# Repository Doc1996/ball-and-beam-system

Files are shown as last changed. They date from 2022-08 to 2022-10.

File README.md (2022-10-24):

# Ball and Beam Control System

<br>

<p align="justify">&nbsp;&nbsp;&nbsp;&nbsp;&nbsp;&nbsp;&nbsp;&nbsp;To examine the possibility of controlling an inherently unstable and nonlinear system, in this project a ball and beam laboratory setup is designed and an appropriate ball position control system is implemented. The design of the laboratory setup includes the selection of the appropriate electronic and mechanical components, design of mechanical components that are not available, production of designed components and assembling all elements of the setup into a whole. The implementation of the ball position control system involves defining the input and output variables of the designed setup, identification of the mathematical model of the setup, designing a suitable variable estimator and designing a controller that will control the position of the ball on the beam.</p>

<br>

## Project workflow

<br>

<b>Step 1.</b>&nbsp;&nbsp;Designing and 3D printing the needed components
<br>
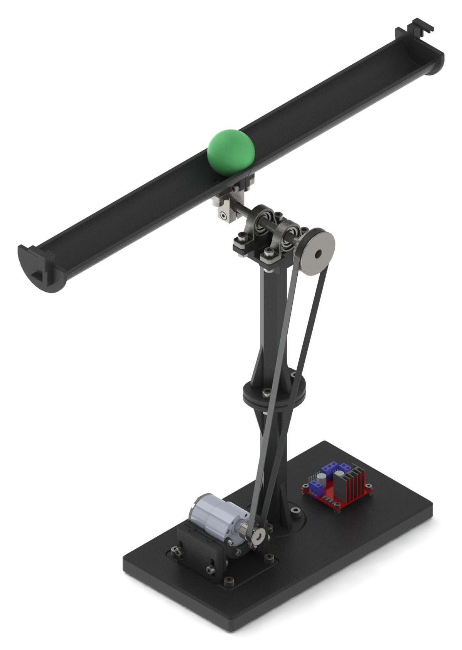
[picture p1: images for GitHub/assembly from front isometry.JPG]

<br>

<b>Step 2.</b>&nbsp;&nbsp;Assembling the components into a system
<br>
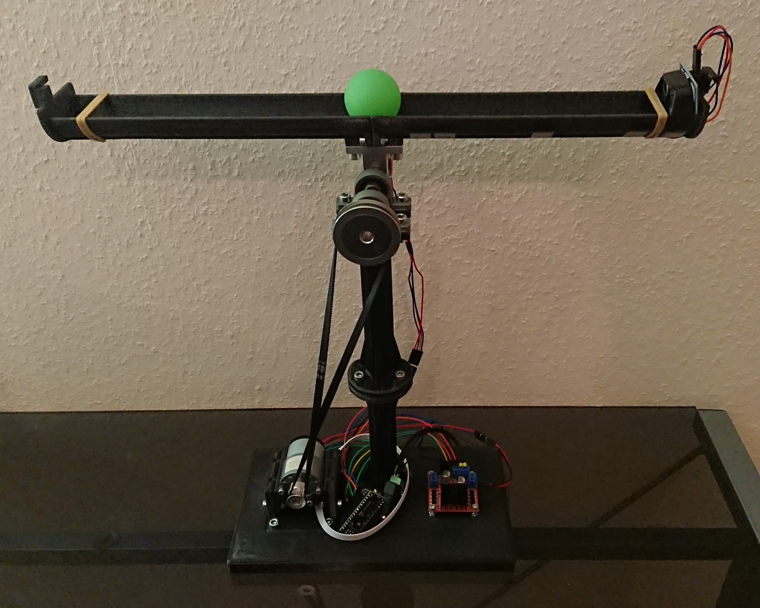
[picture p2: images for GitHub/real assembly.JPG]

<br>

<b>Step 3.</b>&nbsp;&nbsp;Identifying the motor model
<br>
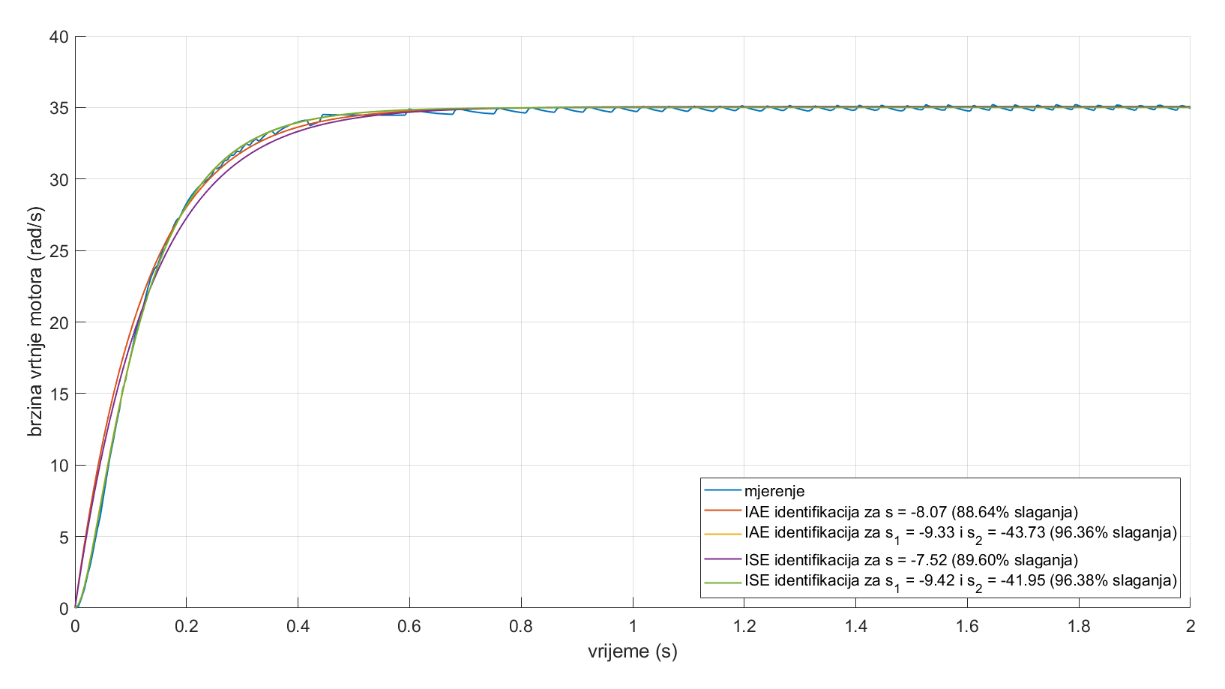
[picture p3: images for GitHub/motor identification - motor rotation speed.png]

<br>

<b>Step 4.</b>&nbsp;&nbsp;Modeling the ball and beam system
<br>
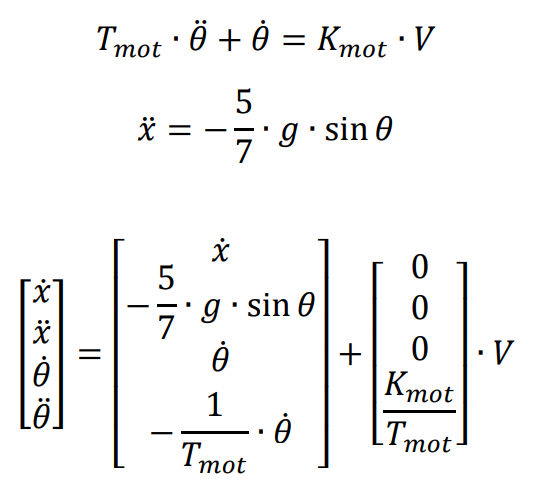
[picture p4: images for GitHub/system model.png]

<br>

<b>Step 5.</b>&nbsp;&nbsp;Designing the both low-pass filtering estimator and extended Kalman filter (EKF)
<br>
<br>

<b>Step 6.</b>&nbsp;&nbsp;Designing the both PD-PD cascade controller and state-space controller
<br>
<br>

<b>Step 7.</b>&nbsp;&nbsp;Modeling the motor static friction
<br>
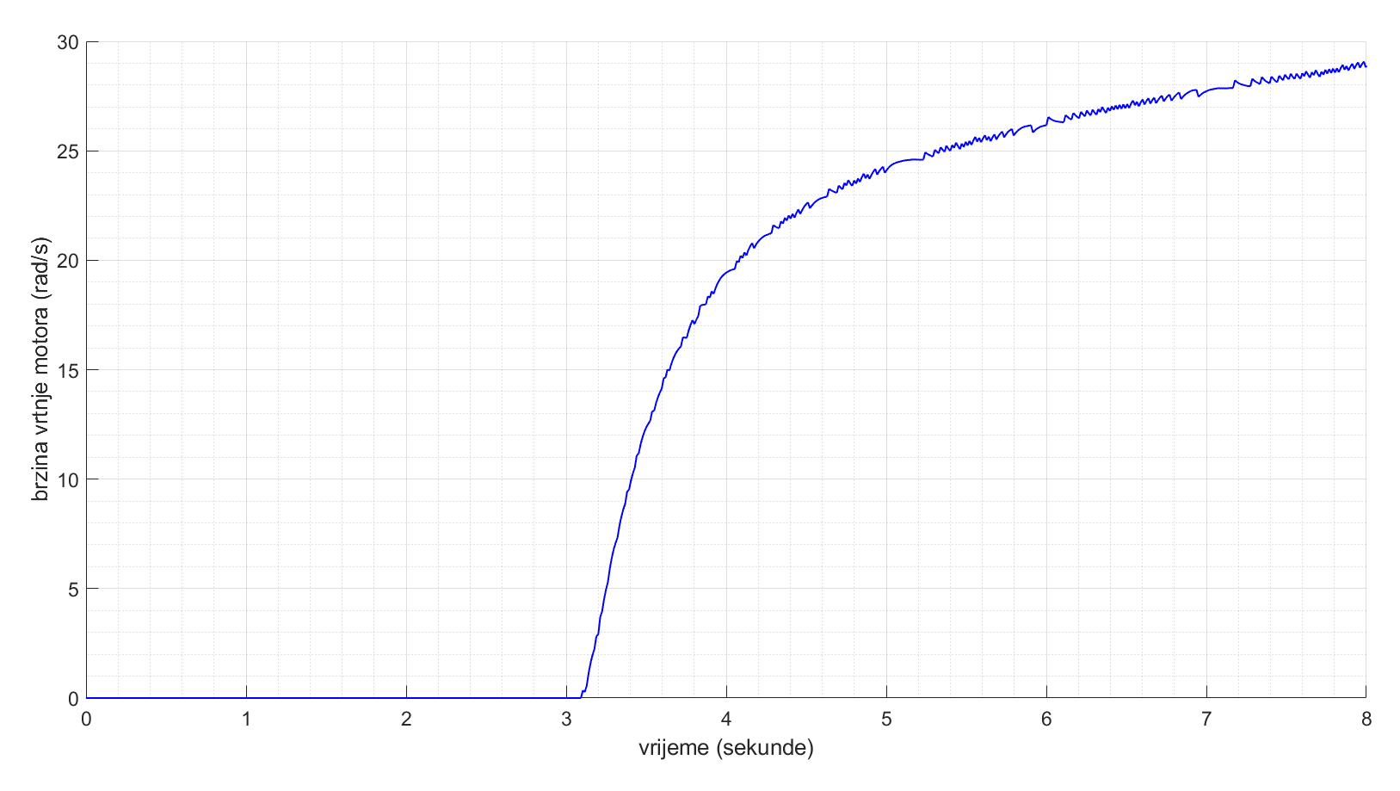
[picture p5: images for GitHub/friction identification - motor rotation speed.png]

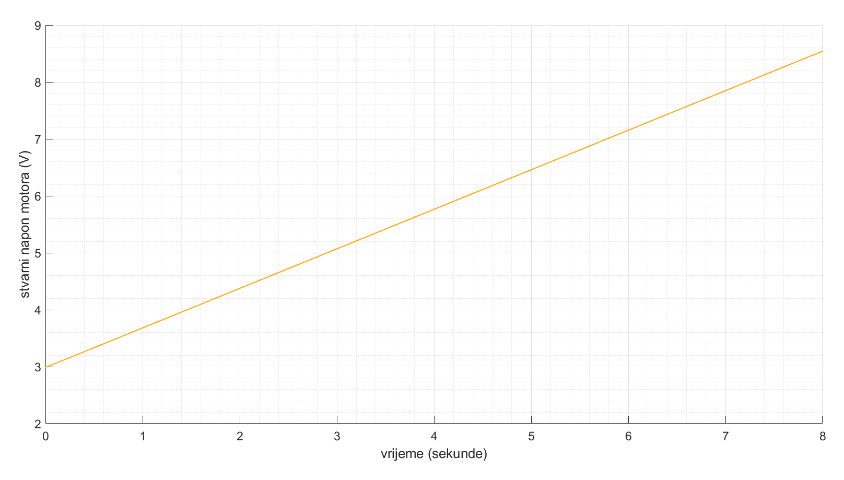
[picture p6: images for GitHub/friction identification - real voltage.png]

<br>

<b>Step 8.</b>&nbsp;&nbsp;Implementing the designed estimators and controllers on the Arduino Uno microcontroller
<br>
<br>

<b>Step 9.</b>&nbsp;&nbsp;Analyzing the results for disturbance compensation (shown for EKF and state-space controller)
<br>
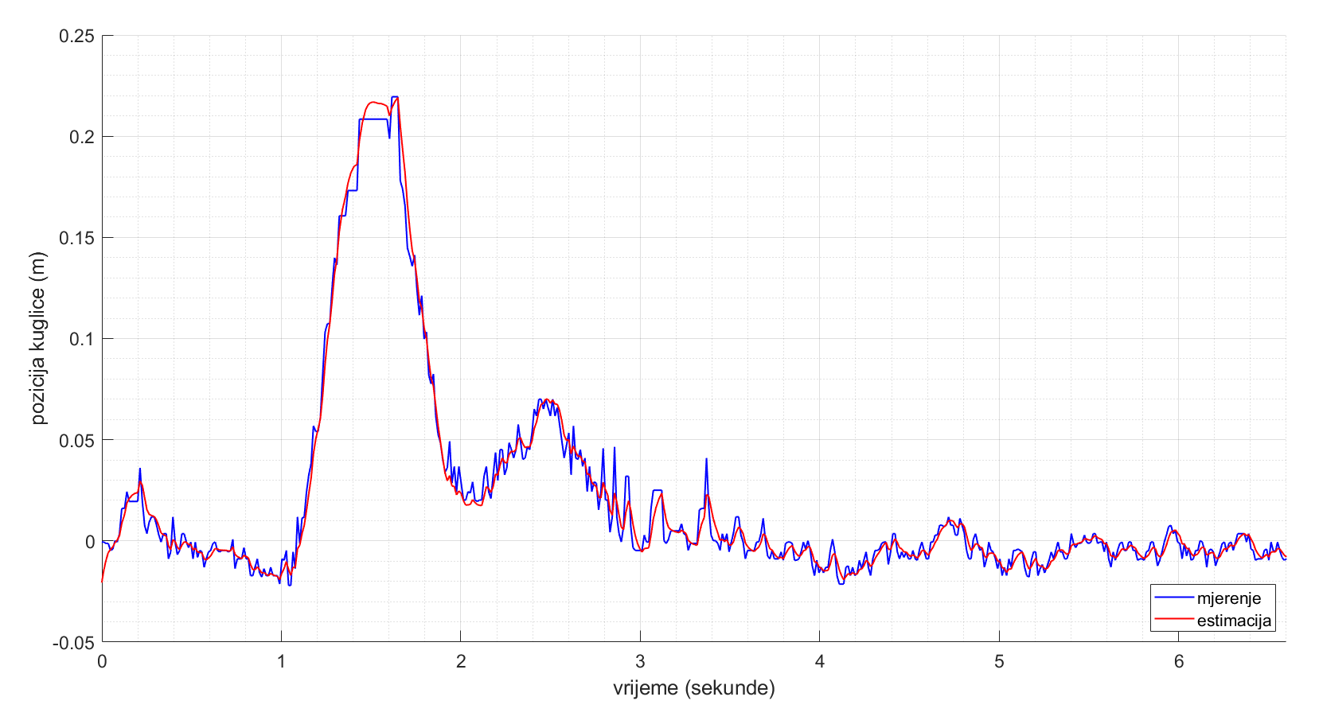
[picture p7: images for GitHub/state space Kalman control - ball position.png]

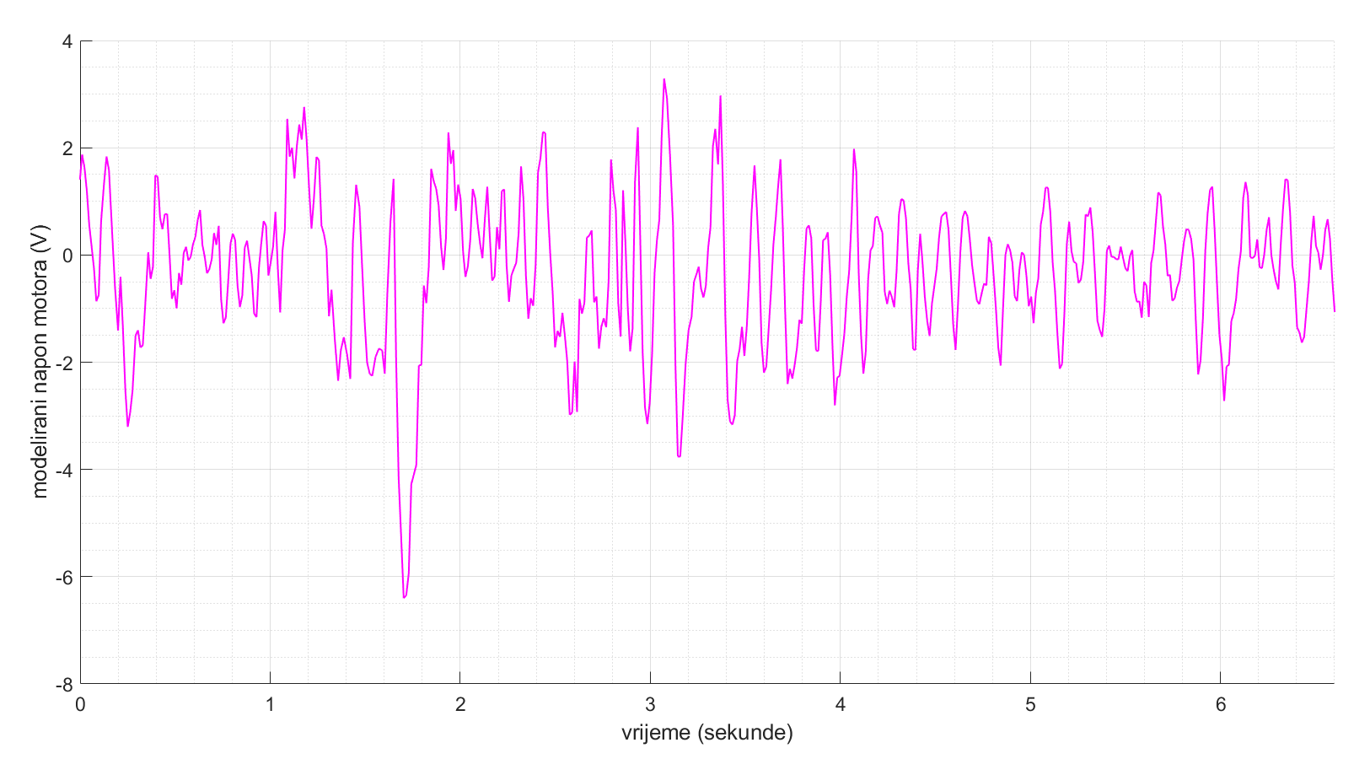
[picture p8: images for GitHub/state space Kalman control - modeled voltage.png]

<br>

<b>Step 10.</b>&nbsp;&nbsp;Analyzing the results for reference tracking (shown for EKF and state-space controller)
<br>
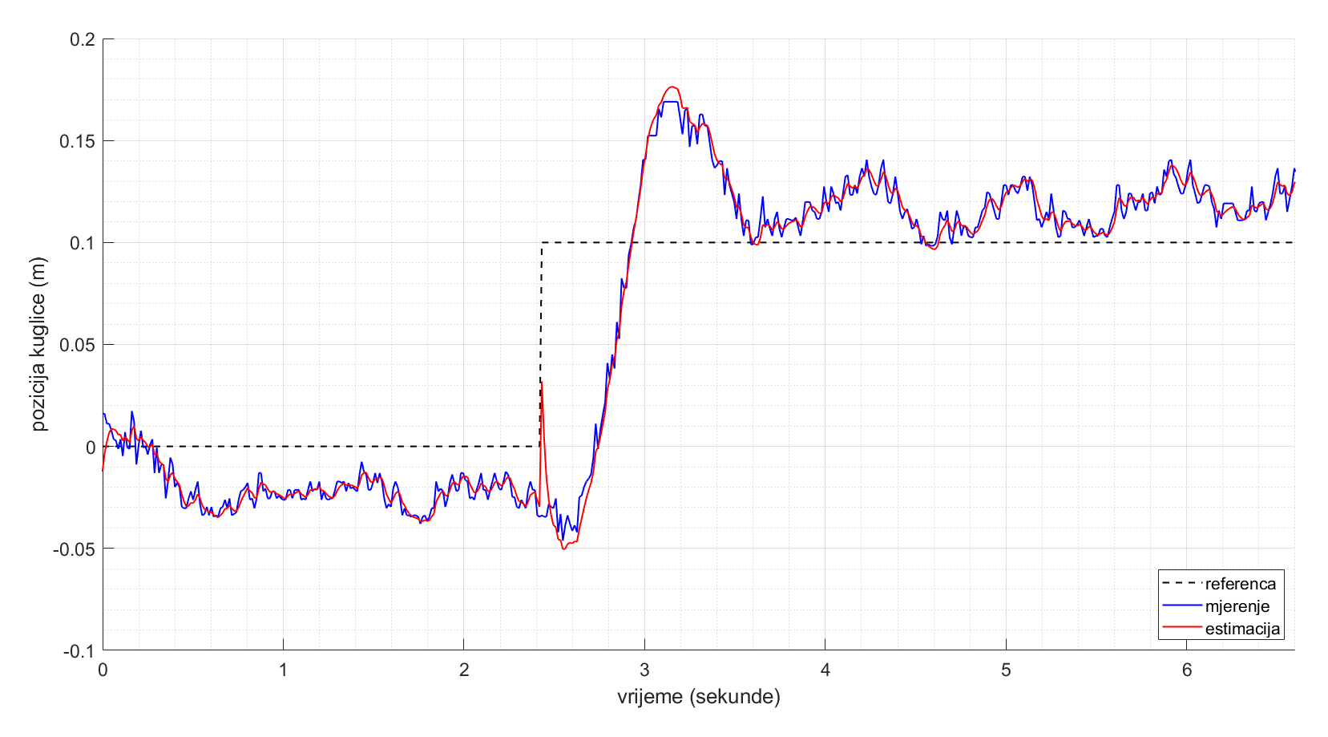
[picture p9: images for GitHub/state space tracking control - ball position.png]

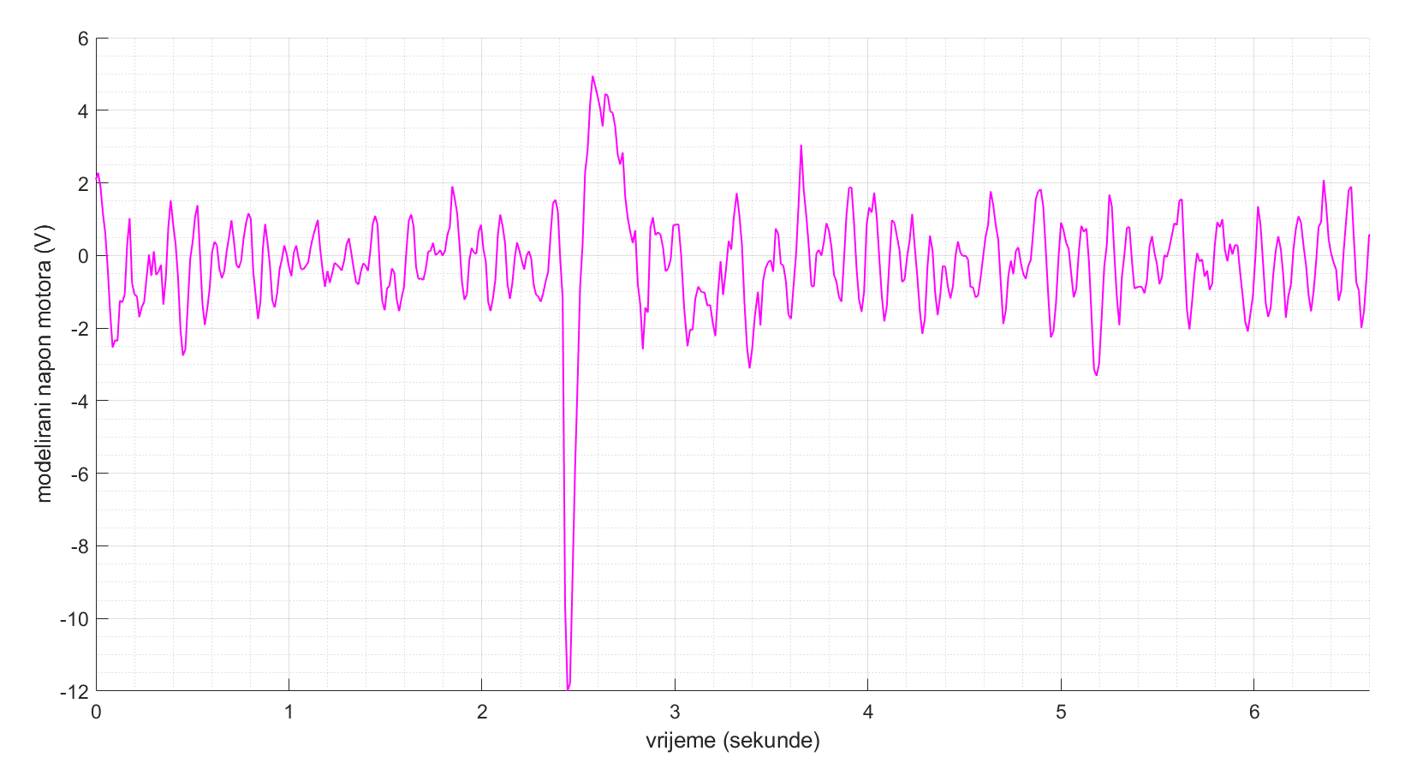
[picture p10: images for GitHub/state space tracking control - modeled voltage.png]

<br>

<b>Step 11.</b>&nbsp;&nbsp;Choosing the system with state-space controller and EKF due to best results
<br>
<br>

## Run the project on Windows

<br>

<b>Step 1.</b>&nbsp;&nbsp;Clone the repository:
<pre>
cd %HOMEPATH%

git clone https://github.com/Doc1996/ball-and-beam-system
</pre>
<br>

<b>Step 2.</b>&nbsp;&nbsp;Setup the Arduino IDE for using the Arduino Uno microcontroller
<br>
<br>

<b>Step 3.</b>&nbsp;&nbsp;Upload the Arduino project <i>system_control</i> to the microcontroller
<br>
<br>

<b>Optional step</b>&nbsp;&nbsp;Run the Matlab script <i>identify_and_control_model.m</i> and examine results
<br>
<br>

<b>Optional step</b>&nbsp;&nbsp;Run the Matlab script <i>plot_record_data.m</i> and examine results
<br>
<br>

## Run the project on Linux

<br>

<b>Step 1.</b>&nbsp;&nbsp;Clone the repository:
<pre>
cd $HOME

git clone https://github.com/Doc1996/ball-and-beam-system
</pre>
<br>

<b>Step 2.</b>&nbsp;&nbsp;Setup the Arduino IDE for using the Arduino Uno microcontroller
<br>
<br>

<b>Step 3.</b>&nbsp;&nbsp;Upload the Arduino project <i>system_control</i> to the microcontroller
<br>
<br>

<b>Optional step</b>&nbsp;&nbsp;Run the Matlab script <i>identify_and_control_model.m</i> and examine results
<br>
<br>

<b>Optional step</b>&nbsp;&nbsp;Run the Matlab script <i>plot_record_data.m</i> and examine results
<br>
<br>

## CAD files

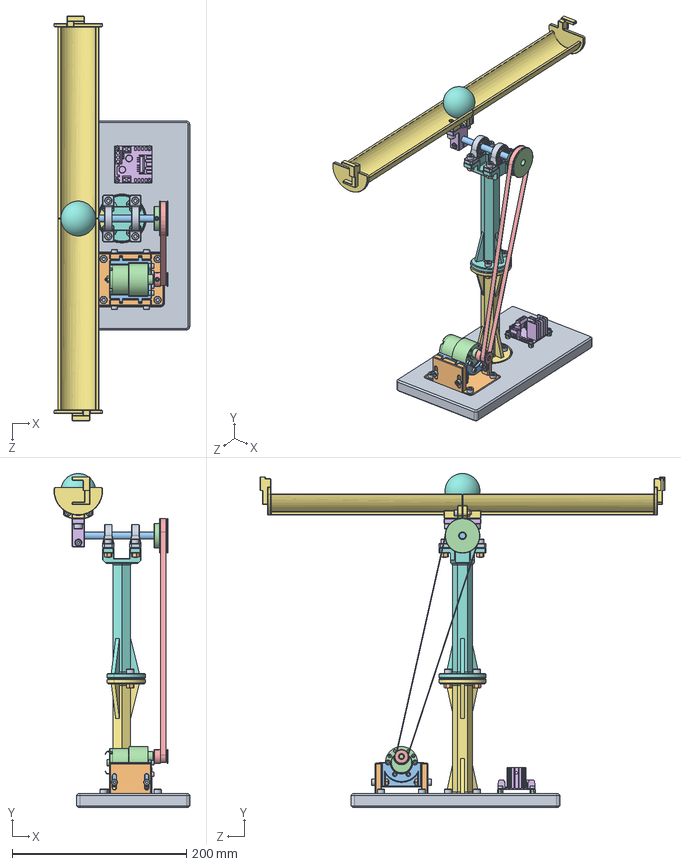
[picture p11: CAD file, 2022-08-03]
ball and beam model/ball and beam assembly.SLDASM
155.7 x 383.4 x 464.4 mm
mount
motor slider
motor frame
JGB37-520 motor
6mm 20-teeth gear
L298N driver
lower pillar
upper pillar
bearing frame x 2
ball bearing x 2
shaft
8mm 60-teeth gear
timing belt
holder
half guide x 2
ball
socket head cap screw_din x 30
hex nut style 1 gradeab_din x 19
socket set screw flat point_din x 4
hex nut style 1 gradeab_iso x 12

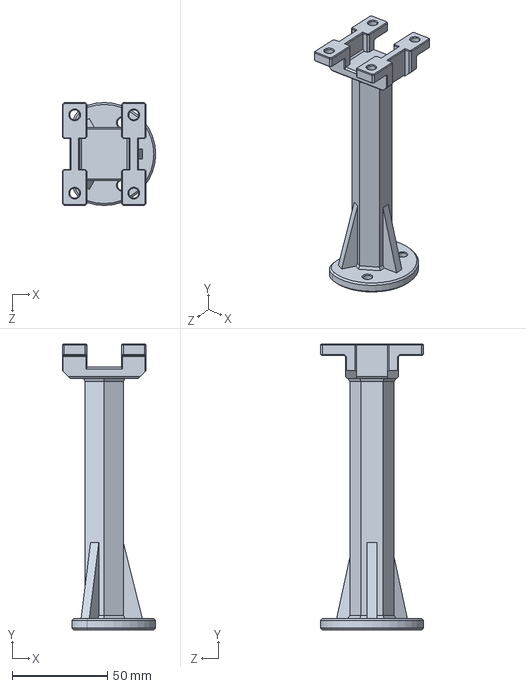
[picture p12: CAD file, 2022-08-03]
ball and beam model/upper pillar.SLDPRT
49.0 x 150.0 x 54.0 mm

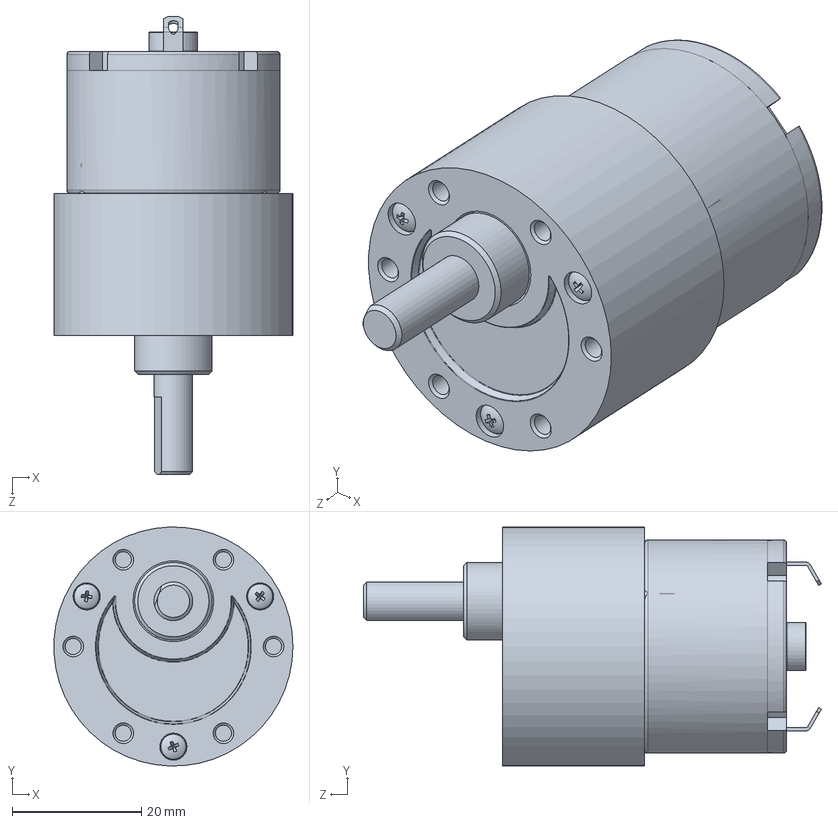
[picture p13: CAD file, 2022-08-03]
ball and beam model/JGB37-520 motor.SLDPRT
37.0 x 37.0 x 70.9 mm

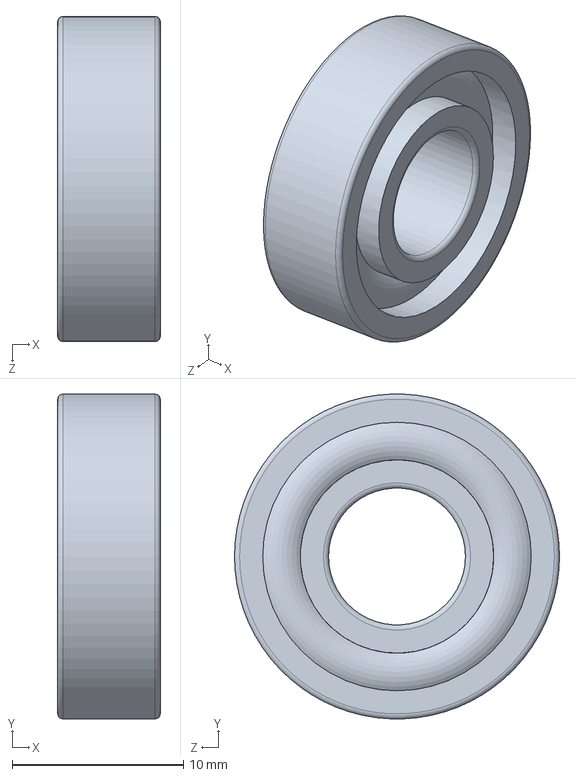
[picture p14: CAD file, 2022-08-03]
ball and beam model/ball bearing.SLDPRT
6.00 x 19.0 x 19.0 mm

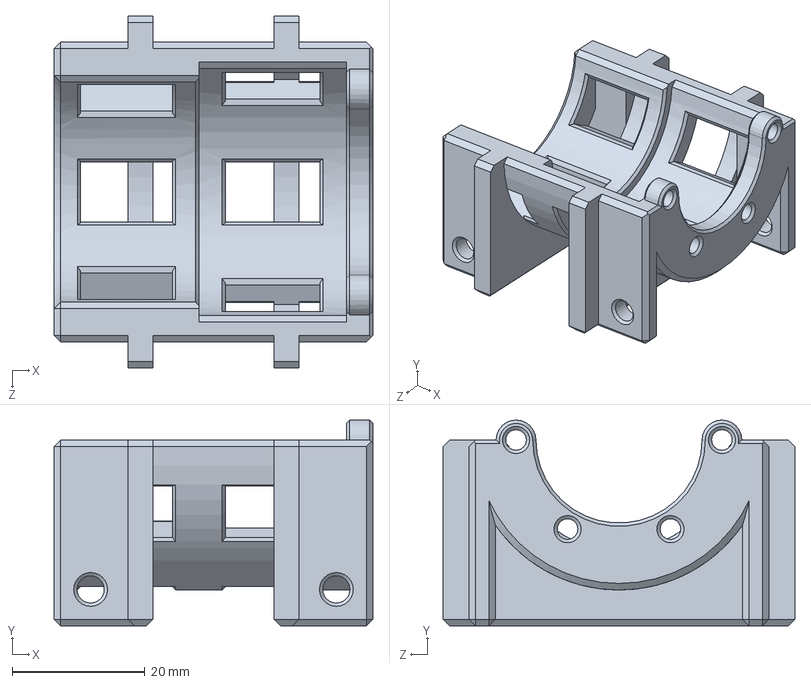
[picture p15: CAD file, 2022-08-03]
ball and beam model/motor frame.SLDPRT
48.0 x 31.0 x 53.0 mm

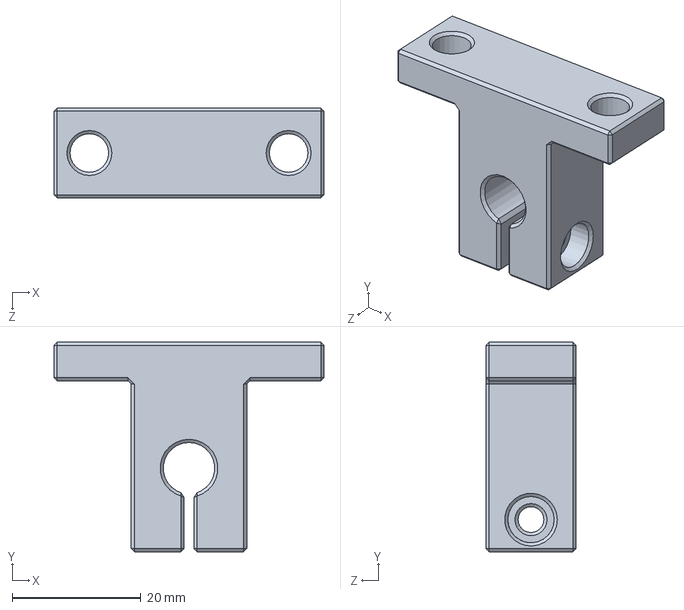
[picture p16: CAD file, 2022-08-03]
ball and beam model/holder.SLDPRT
42.0 x 32.6 x 14.0 mm

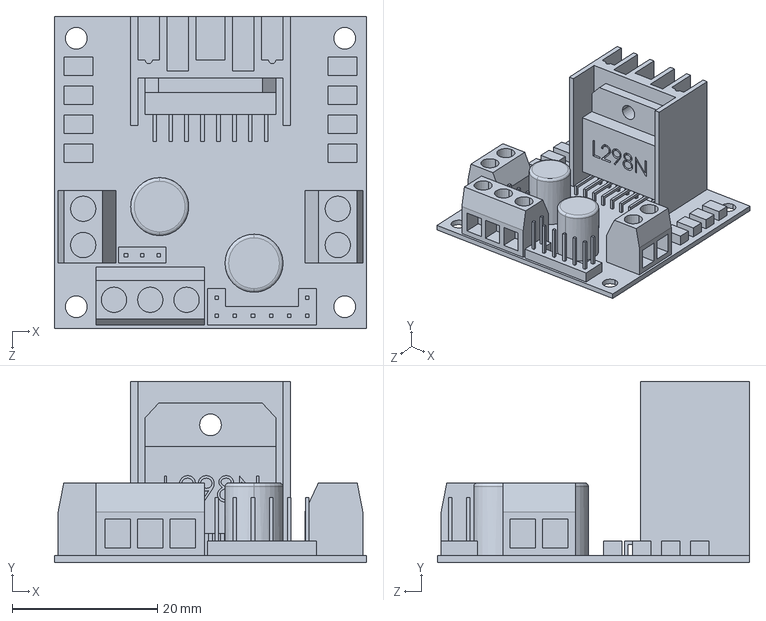
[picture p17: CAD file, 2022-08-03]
ball and beam model/L298N driver.SLDPRT
43.0 x 25.0 x 43.0 mm

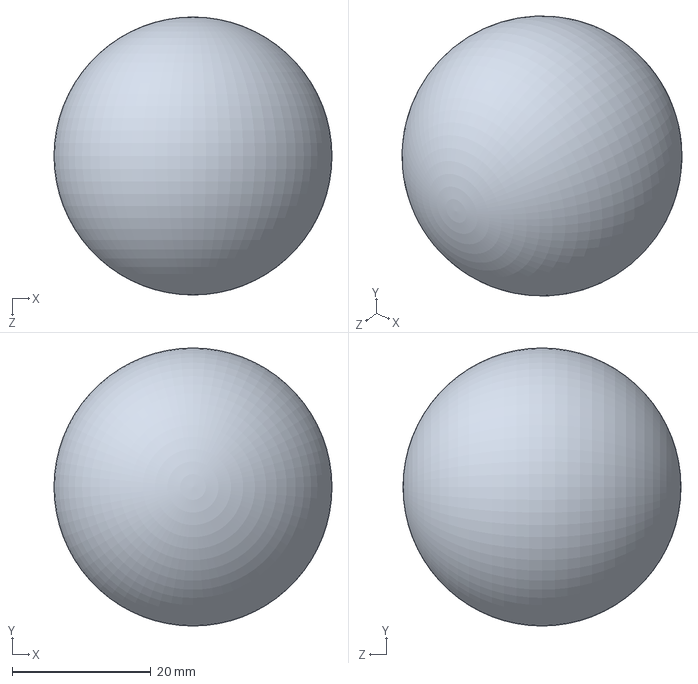
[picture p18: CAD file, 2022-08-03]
ball and beam model/ball.SLDPRT
40.0 x 40.0 x 40.0 mm

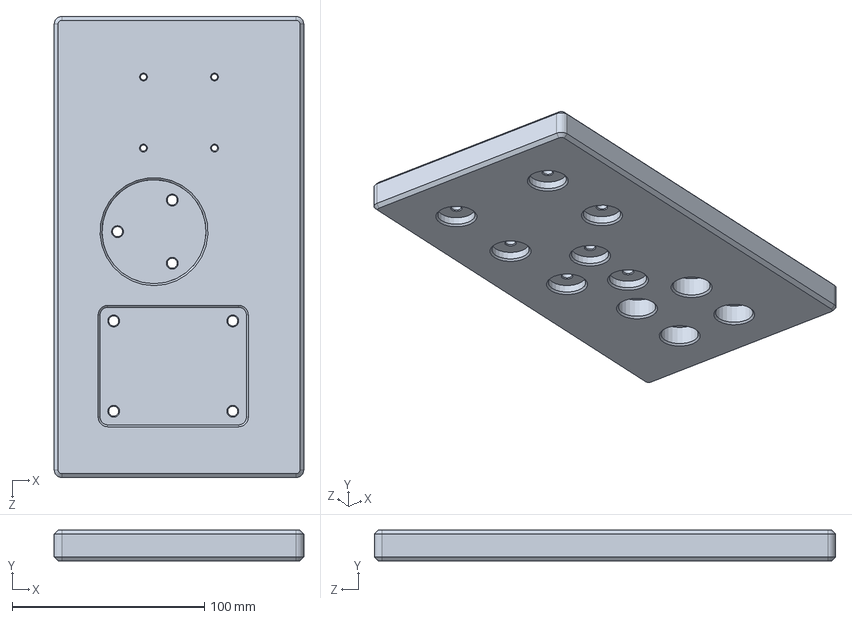
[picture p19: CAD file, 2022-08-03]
ball and beam model/mount.SLDPRT
130.0 x 16.0 x 240.0 mm

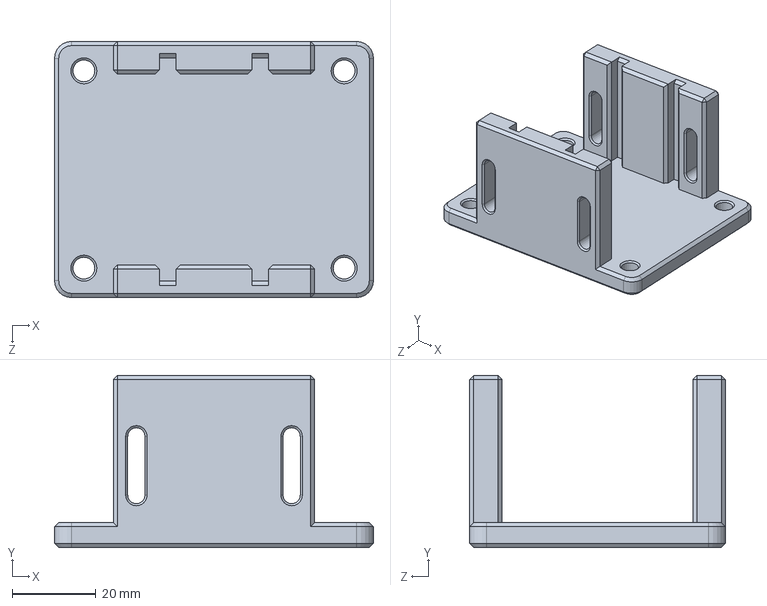
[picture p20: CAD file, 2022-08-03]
ball and beam model/motor slider.SLDPRT
76.0 x 41.0 x 61.0 mm

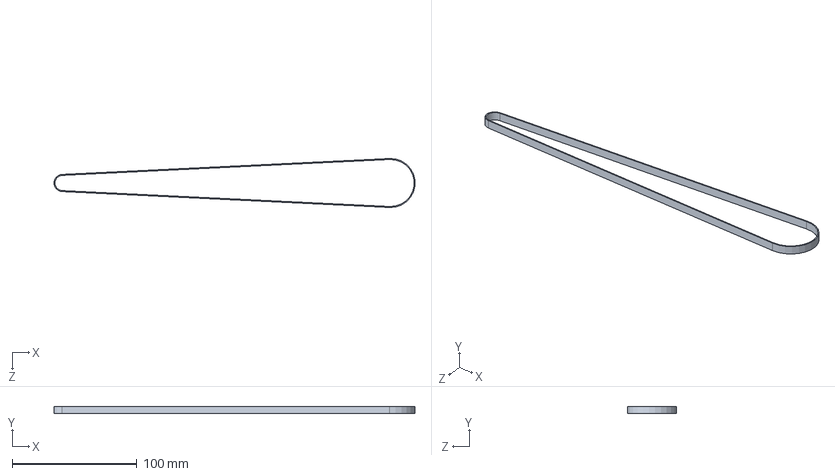
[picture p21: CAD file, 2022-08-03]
ball and beam model/timing belt.SLDPRT
289.4 x 6.00 x 39.3 mm

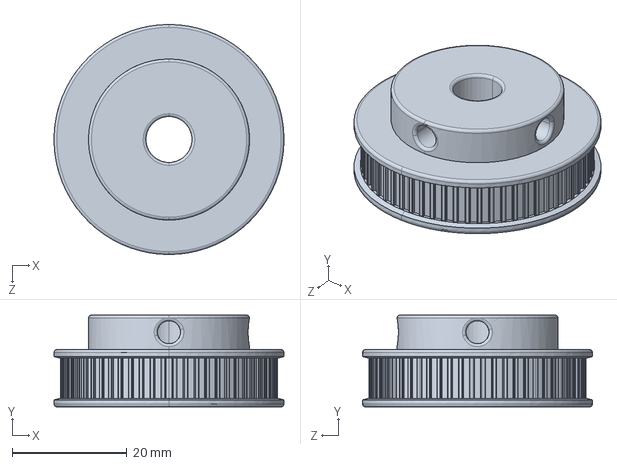
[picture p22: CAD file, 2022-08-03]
ball and beam model/8mm 60-teeth gear.SLDPRT
40.0 x 16.0 x 40.0 mm

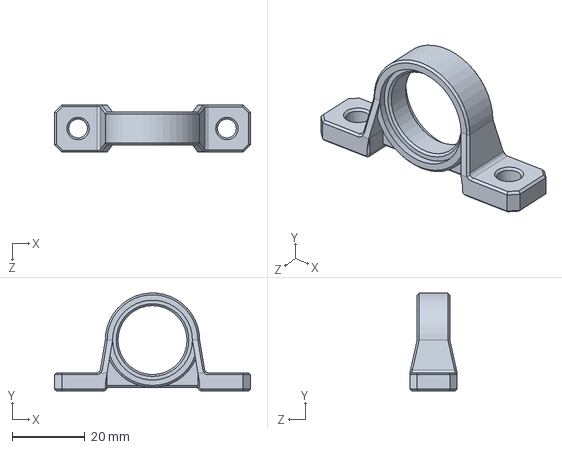
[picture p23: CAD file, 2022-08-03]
ball and beam model/bearing frame.SLDPRT
54.0 x 27.0 x 13.0 mm

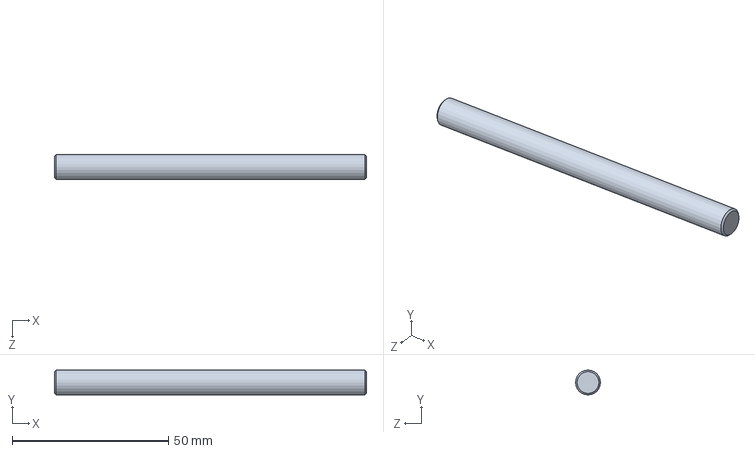
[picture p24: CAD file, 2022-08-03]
ball and beam model/shaft.SLDPRT
100.0 x 8.00 x 8.00 mm

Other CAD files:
ball and beam model/6mm 20-teeth gear.SLDPRT
ball and beam model/half guide.SLDPRT
ball and beam model/lower pillar.SLDPRT

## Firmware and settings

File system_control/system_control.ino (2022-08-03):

#include <EEPROM.h>
#include <BasicLinearAlgebra.h>
#include <NewPing.h>

#define ENCODER_ENCA_PIN 2
#define ENCODER_ENCB_PIN 3

#define MOTOR_ENA_PIN 5
#define MOTOR_IN1_PIN 6
#define MOTOR_IN2_PIN 7

#define ULTRASOUND_ECHO_PIN 8
#define ULTRASOUND_TRIG_PIN 9

#define SERIAL_BAUD_RATE 115200
#define SERIAL_SCALING_FACTOR 1000.0
#define WORKING_STATE_ADDRESS 0

#define LED_BLINKING_TIME_IN_SEC 0.15
#define SAMPLE_TIME_IN_SEC 0.012
#define REF_COMPLETE_CYCLE_TIME_IN_SEC 5.0

#define STARTING_DELAY_TIME_IN_SEC 1.0
#define MIN_WARMUP_TIME_IN_SEC 0.5
#define MAX_WORKING_TIME_IN_SEC (MIN_WARMUP_TIME_IN_SEC + 600.0)

#define MICROSEC_TO_MILLISEC_FACTOR (1.0 / 1000.0)
#define MILLISEC_TO_SEC_FACTOR (1.0 / 1000.0)
#define SEC_TO_MIN_FACTOR (1.0 / 60.0)

#define MILLIMETER_TO_METER_FACTOR (1.0 / 1000.0)
#define ROT_PER_MIN_TO_ROT_PER_SEC_FACTOR (1.0 / 60.0)
#define ROT_TO_RAD_FACTOR (2 * PI_NUMBER)
#define DEG_TO_RAD_FACTOR (2 * PI_NUMBER / 180.0)

#define PI_NUMBER 3.14159
#define EULER_NUMBER 2.71828
#define SOUND_VEL_IN_METERS_PER_SEC 346.0

#define ENCODER_COUNTS_RATIO 17.0
#define MOTOR_GEAR_RATIO 18.75
#define BEAM_GEAR_RATIO 3.0

#define LIMIT_BEAM_ROTATION_DEG (20.0 * 1000.0)
#define LIMIT_MOTOR_ROTATION_RAD (LIMIT_BEAM_ROTATION_DEG * BEAM_GEAR_RATIO * DEG_TO_RAD_FACTOR)
#define MAX_ROTATION_VEL (330.0 * SEC_TO_MIN_FACTOR * ROT_TO_RAD_FACTOR)

#define THRESHOLD_PWM_SIGNAL 5.0
#define MIN_PWM_SIGNAL 120.0
#define MAX_PWM_SIGNAL 255.0

#define HALF_BEAM_LENGTH_IN_METERS 0.220
#define INITIAL_DISTANCE_IN_METERS 0.008
#define BALL_RADIUS_IN_METERS 0.020

#define CENTER_DISTANCE_IN_METERS (HALF_BEAM_LENGTH_IN_METERS + INITIAL_DISTANCE_IN_METERS - BALL_RADIUS_IN_METERS)
#define MAX_DISTANCE_IN_METERS (CENTER_DISTANCE_IN_METERS + HALF_BEAM_LENGTH_IN_METERS)

#define U_ORDER 1
#define N_ORDER 4
#define Y_ORDER 2




enum controller_enum {ControllerStopped, ControllerRotVelocityNone, ControllerRotationPD, ControllerOffsetCascadePD, ControllerOffsetStateSpace};
enum estimator_enum {EstimatorUndefined, EstimatorFiltering, EstimatorKalman};
enum tracking_enum {TrackingUndefined, TrackingKalmanNone, TrackingKalmanOffset};

controller_enum controller_type;
estimator_enum estimator_type;
tracking_enum tracking_type;

NewPing ultrasound_sensor(ULTRASOUND_TRIG_PIN, ULTRASOUND_ECHO_PIN, (int) (MAX_DISTANCE_IN_METERS / MILLIMETER_TO_METER_FACTOR));

int prev_working_state_num;
int working_state_num;

float time_in_millisec;
float time_in_sec;
float prev_time_in_sec = 0.0;
float delta_time_in_sec;

float ref_cycling_time_in_sec = 0.0;
int ref_cycling_state_num = 0;

int PRBS_counter = 0;

// variables used in interrupts must be declared volatile
volatile float readed_increments = 0.0;
volatile float readed_distance = 0.0;

float raw_rotation;
float prev_raw_rotation = 0.0;
float rotation;
float prev_rotation = 0.0;

float raw_rotation_vel;
float rotation_vel;
float prev_rotation_vel = 0.0;

float raw_offset;
float prev_raw_offset = 0.0;
float offset;
float prev_offset = 0.0;

float raw_offset_vel;
float offset_vel;
float prev_offset_vel = 0.0;

float raw_error;
float prev_raw_error = 0.0;
float error;
float prev_error = 0.0;

float raw_error_vel;
float error_vel;
float prev_error_vel = 0.0;

float raw_inner_error;
float inner_error;
float prev_inner_error = 0.0;

float raw_inner_error_vel;
float inner_error_vel;
float prev_inner_error_vel = 0.0;

float ref_rotation;
float ref_rotation_vel;
float ref_offset;

float pwm_model_value;
float pwm_real_value;



BLA::Matrix<U_ORDER> u_k = 0.0;

BLA::Matrix<N_ORDER> x_hat_k = {0.0, 0.0, 0.0, 0.0};
BLA::Matrix<N_ORDER> x_hat_m_k;

BLA::Matrix<N_ORDER> x_dev_k = {0.0, 0.0, 0.0, 0.0};

BLA::Matrix<Y_ORDER> y_k;

BLA::Matrix<N_ORDER, N_ORDER> Phi_k;
BLA::Matrix<Y_ORDER, N_ORDER> H_k;

BLA::Matrix<N_ORDER, 1> f_hat_k;
BLA::Matrix<N_ORDER, U_ORDER> g_hat_k;

BLA::Matrix<U_ORDER, N_ORDER> K_control_k;

BLA::Matrix<N_ORDER, Y_ORDER> K_kalman_k;

BLA::Matrix<N_ORDER, N_ORDER> I_k = {1.0, 0.0, 0.0, 0.0,
                                     0.0, 1.0, 0.0, 0.0,
                                     0.0, 0.0, 1.0, 0.0,
                                     0.0, 0.0, 0.0, 1.0
                                    };

BLA::Matrix<N_ORDER, N_ORDER> P_k = {x_dev_k(0),        0.0,        0.0,        0.0,
                                            0.0, x_dev_k(1),        0.0,        0.0,
                                            0.0,        0.0, x_dev_k(2),        0.0,
                                            0.0,        0.0,        0.0, x_dev_k(3)
                                    };
BLA::Matrix<N_ORDER, N_ORDER> P_m_k;

BLA::Matrix<N_ORDER, N_ORDER> Q_k = {0.001, 0.0,   0.0, 0.0,
                                       0.0, 0.2,   0.0, 0.0,
                                       0.0, 0.0, 0.001, 0.0,
                                       0.0, 0.0,   0.0, 8.0
                                   };

BLA::Matrix<Y_ORDER, Y_ORDER> R_k = {0.01,  0.0,
                                      0.0, 0.01
                                    };



float F_PREV_ERROR = 0.85;
float F_RAW_ERROR = (1.0 - F_PREV_ERROR);
float F_PREV_ERROR_VEL = 0.9;
float F_RAW_ERROR_VEL = (1.0 - F_PREV_ERROR_VEL);

float F_PREV_INNER_ERROR = 0.35;
float F_RAW_INNER_ERROR = (1.0 - F_PREV_INNER_ERROR);
float F_PREV_INNER_ERR_VEL = 0.45;
float F_RAW_INNER_ERR_VEL = (1.0 - F_PREV_INNER_ERR_VEL);

float K_CRIT_ERROR = -4.0;
float T_CRIT_ERROR = 2.5;
float K_PROP_ERROR = (0.8 * K_CRIT_ERROR);
float K_DER_ERROR = (0.15 * K_CRIT_ERROR * T_CRIT_ERROR);

float K_CRIT_INNER_ERROR = 230.0;
float T_CRIT_INNER_ERROR = 0.3;
float K_PROP_INNER_ERROR = (0.8 * K_CRIT_INNER_ERROR);
float K_DER_INNER_ERROR = (0.15 * K_CRIT_INNER_ERROR * T_CRIT_INNER_ERROR);

float F_PREV_OFFSET = 0.85;
float F_RAW_OFFSET = (1.0 - F_PREV_OFFSET);
float F_PREV_OFFSET_VEL = 0.9;
float F_RAW_OFFSET_VEL = (1.0 - F_PREV_OFFSET_VEL);

float F_PREV_ROTATION = 0.35;
float F_RAW_ROTATION = (1.0 - F_PREV_ROTATION);
float F_PREV_ROT_VEL = 0.45;
float F_RAW_ROT_VEL = (1.0 - F_PREV_ROT_VEL);

bool plot_time_data_bool = true;
bool inverted_belt_bool = true;




void setup() {
  Serial.begin(SERIAL_BAUD_RATE);

  pinMode(ENCODER_ENCA_PIN, INPUT);
  pinMode(ENCODER_ENCB_PIN, INPUT);

  pinMode(LED_BUILTIN, OUTPUT);

  pinMode(MOTOR_ENA_PIN, OUTPUT);
  pinMode(MOTOR_IN1_PIN, OUTPUT);
  pinMode(MOTOR_IN2_PIN, OUTPUT);

  pinMode(ULTRASOUND_ECHO_PIN, INPUT);
  pinMode(ULTRASOUND_TRIG_PIN, OUTPUT);

  attachInterrupt(digitalPinToInterrupt(ENCODER_ENCB_PIN), read_encoder_inc_change, RISING);

  stop_motor();


  prev_working_state_num = EEPROM.read(WORKING_STATE_ADDRESS); 

  if (prev_working_state_num < 4) {
    working_state_num = prev_working_state_num + 1;
  }
  else {
    working_state_num = 0;
  }

  EEPROM.write(WORKING_STATE_ADDRESS, working_state_num);

  if (working_state_num == 0) {
    controller_type = ControllerStopped;
    estimator_type = EstimatorUndefined;
    tracking_type = TrackingUndefined;
  }
  else if (working_state_num == 1) {
    controller_type = ControllerOffsetCascadePD;
    estimator_type = EstimatorUndefined;
    tracking_type = TrackingUndefined;
  }
  else if (working_state_num == 2) {
    controller_type = ControllerOffsetStateSpace;
    estimator_type = EstimatorFiltering;
    tracking_type = TrackingUndefined;
  }
  else if (working_state_num == 3) {
    controller_type = ControllerOffsetStateSpace;
    estimator_type = EstimatorKalman;
    tracking_type = TrackingKalmanNone;
  }
  else if (working_state_num == 4) {
    controller_type = ControllerOffsetStateSpace;
    estimator_type = EstimatorKalman;
    tracking_type = TrackingKalmanOffset;
  }


  blink_LED();
  blink_LED();

  delay((int) (2 * LED_BLINKING_TIME_IN_SEC / MILLISEC_TO_SEC_FACTOR));

  for (int counter = 0; counter < working_state_num; counter++) {
    blink_LED();
  }
  
  delay((int) (STARTING_DELAY_TIME_IN_SEC / MILLISEC_TO_SEC_FACTOR));
}




void loop() {
  time_in_millisec = (float) micros() * MICROSEC_TO_MILLISEC_FACTOR;
  time_in_sec = time_in_millisec * MILLISEC_TO_SEC_FACTOR;


  if (time_in_sec - prev_time_in_sec >= SAMPLE_TIME_IN_SEC) {

    delta_time_in_sec = time_in_sec - prev_time_in_sec;
    prev_time_in_sec = time_in_sec;


    if (time_in_sec <= MAX_WORKING_TIME_IN_SEC) {

      noInterrupts();  // disable interrupts before accessing raw increment change
      raw_rotation = readed_increments * ROT_TO_RAD_FACTOR / (ENCODER_COUNTS_RATIO * MOTOR_GEAR_RATIO);
      interrupts();  // enable interrupts after accessing raw increment change

      if (inverted_belt_bool == true) {
        raw_rotation = - raw_rotation;
      }


      ultrasound_sensor.ping_timer(read_ultrasound_distance);
      raw_offset = readed_distance - CENTER_DISTANCE_IN_METERS;

      if (raw_offset >= HALF_BEAM_LENGTH_IN_METERS) {
        raw_offset = prev_raw_offset;
      }

      prev_raw_offset = raw_offset;


      if (time_in_sec >= MIN_WARMUP_TIME_IN_SEC) {

        if ((raw_rotation >= - LIMIT_MOTOR_ROTATION_RAD) && (raw_rotation <= LIMIT_MOTOR_ROTATION_RAD)) {

          if (controller_type == ControllerStopped) {
      	    pwm_model_value = 0.0;
      	    pwm_real_value = pwm_model_value;
	        }


          else if (controller_type == ControllerRotVelocityNone) {
            ref_rotation_vel = 0.0;

            raw_rotation_vel = (raw_rotation - prev_raw_rotation) / delta_time_in_sec;
            prev_raw_rotation = raw_rotation;

            pwm_model_value = ref_rotation_vel / MAX_ROTATION_VEL * MAX_PWM_SIGNAL;
            pwm_real_value = pwm_model_value;
          }


          else if (controller_type == ControllerRotationPD) {
            ref_rotation = 0.0;
            raw_error = ref_rotation - raw_rotation;

            raw_error_vel = (raw_error - prev_raw_error) / delta_time_in_sec;
            prev_raw_error = raw_error;

            pwm_model_value = K_PROP_INNER_ERROR * raw_error + K_DER_INNER_ERROR * raw_error_vel;
            pwm_real_value = get_dead_zone_compensated_value(pwm_model_value);
          }


          else if (controller_type == ControllerOffsetCascadePD) {
            ref_offset = 0.0;
            raw_error = ref_offset - raw_offset;


            error = F_PREV_ERROR * prev_error + F_RAW_ERROR * raw_error;
            raw_error_vel = (error - prev_error) / delta_time_in_sec;
            prev_error = error;

            error_vel = F_PREV_ERROR_VEL * prev_error_vel + F_RAW_ERROR_VEL * raw_error_vel;
            prev_error_vel = error_vel;

            ref_rotation = K_PROP_ERROR * error + K_DER_ERROR * error_vel;
            raw_inner_error = ref_rotation - raw_rotation;


            inner_error = F_PREV_INNER_ERROR * prev_inner_error + F_RAW_INNER_ERROR * raw_inner_error;
            raw_inner_error_vel = (inner_error - prev_inner_error) / delta_time_in_sec;
            prev_inner_error = inner_error;

            inner_error_vel = F_PREV_INNER_ERR_VEL * prev_inner_error_vel + F_RAW_INNER_ERR_VEL * raw_inner_error_vel;
            prev_inner_error_vel = inner_error_vel;

            pwm_model_value = K_PROP_INNER_ERROR * inner_error + K_DER_INNER_ERROR * inner_error_vel;
            pwm_real_value = get_dead_zone_compensated_value(pwm_model_value);
          }


          else if (controller_type == ControllerOffsetStateSpace) {
            if (tracking_type == TrackingKalmanNone) {
              ref_offset = 0.0;

              y_k = {raw_offset, raw_rotation};
            }

            else if (tracking_type == TrackingKalmanOffset) {
              if (ref_cycling_time_in_sec < REF_COMPLETE_CYCLE_TIME_IN_SEC) {
                ref_cycling_time_in_sec = ref_cycling_time_in_sec + delta_time_in_sec;
              }
              else {
                ref_cycling_time_in_sec = 0.0;
                
                if (ref_cycling_state_num < 3) {
                  ref_cycling_state_num = ref_cycling_state_num + 1;
                }
                else {
                  ref_cycling_state_num = 0;
                }
              }

              if (ref_cycling_state_num == 0) {
                ref_offset = 0.0;
              }
              else if (ref_cycling_state_num == 1) {
                ref_offset = 0.1;
              }
              else if (ref_cycling_state_num == 2) {
                ref_offset = 0.0;
              }
              else if (ref_cycling_state_num == 3) {
                ref_offset = -0.1;
              }

              y_k = {raw_offset - ref_offset, raw_rotation};
            }


            if (estimator_type == EstimatorFiltering) {
              offset = F_PREV_ERROR * prev_offset + F_RAW_ERROR * raw_offset;
              raw_offset_vel = (offset - prev_offset) / delta_time_in_sec;
              prev_offset = offset;

              offset_vel = F_PREV_ERROR_VEL * prev_offset_vel + F_RAW_ERROR_VEL * raw_offset_vel;
              prev_offset_vel = offset_vel;


              rotation = F_PREV_INNER_ERROR * prev_rotation + F_RAW_INNER_ERROR * raw_rotation;
              raw_rotation_vel = (rotation - prev_rotation) / delta_time_in_sec;
              prev_rotation = rotation;

              rotation_vel = F_PREV_INNER_ERR_VEL * prev_rotation_vel + F_RAW_INNER_ERR_VEL * raw_rotation_vel;
              prev_rotation_vel = rotation_vel;


              x_hat_k = {offset, offset_vel, rotation, rotation_vel};

              K_control_k = {-700.0, -450.0, 250.0, 10.0};
            }


            else if (estimator_type == EstimatorKalman) {
              Phi_k = {1.0, 0.012, 0.0,   0.0,
                       0.0,   1.0, 0.0,   0.0,
                       0.0,   0.0, 1.0, 0.012,
                       0.0,   0.0, 0.0,   1.0
                      };

              H_k = {1.0, 0.0, 0.0, 0.0,
                     0.0, 0.0, 1.0, 0.0
                    };

              f_hat_k = {x_hat_k(1),
                                0.0,
                         x_hat_k(3),
                                0.0
                        };

              g_hat_k = {   0.0,
                            0.0,
                            0.0,
                         1.0933
                        };

              x_hat_m_k = x_hat_k + (f_hat_k + g_hat_k * u_k) * delta_time_in_sec;

              P_m_k = Phi_k * P_k * ~Phi_k + Q_k;
              K_kalman_k = P_m_k * ~H_k * BLA::Inverse((H_k * P_m_k * ~H_k + R_k));
              P_k = (I_k - K_kalman_k * H_k) * P_m_k * ~(I_k - K_kalman_k * H_k) + K_kalman_k * R_k * ~K_kalman_k;

              x_hat_k = x_hat_m_k + K_kalman_k * (y_k - H_k * x_hat_m_k);

              K_control_k = {-700.0, -400.0, 250.0, 15.0};
            }


            u_k = - K_control_k * x_hat_k;

            pwm_model_value = u_k(0);
            pwm_real_value = get_dead_zone_compensated_value(pwm_model_value);
          }


          if (pwm_real_value <= - MAX_PWM_SIGNAL) {
            pwm_real_value = - MAX_PWM_SIGNAL;
          }
          else if (pwm_real_value >= MAX_PWM_SIGNAL) {
            pwm_real_value = MAX_PWM_SIGNAL;
          }

          if (inverted_belt_bool == true) {
            pwm_real_value = - pwm_real_value;
          }

          drive_motor(pwm_real_value);
        }

        else {
          stop_motor();
        }


        if (plot_time_data_bool == true) {
          print_scaled_to_serial(time_in_millisec / SERIAL_SCALING_FACTOR);
        }


        if (controller_type == ControllerRotVelocityNone) {
          print_scaled_to_serial(ref_rotation_vel);

          print_scaled_to_serial(raw_rotation_vel);
        }

        else if (controller_type == ControllerRotationPD) {
          print_scaled_to_serial(ref_rotation);
          
          print_scaled_to_serial(raw_error);
          print_scaled_to_serial(raw_error_vel);
        }

        else if (controller_type == ControllerOffsetCascadePD) {
          print_scaled_to_serial(ref_offset);

          print_scaled_to_serial(raw_error);
          print_scaled_to_serial(error);

          print_scaled_to_serial(raw_error_vel);
          print_scaled_to_serial(error_vel);

          print_scaled_to_serial(raw_inner_error);
          print_scaled_to_serial(inner_error);

          print_scaled_to_serial(raw_inner_error_vel);
          print_scaled_to_serial(inner_error_vel);
        }

        else if (controller_type == ControllerOffsetStateSpace) {
          print_scaled_to_serial(ref_offset);

          print_scaled_to_serial(raw_offset);
          print_scaled_to_serial(x_hat_k(0) + ref_offset);

          print_scaled_to_serial(x_hat_k(1));

          print_scaled_to_serial(raw_rotation);
          print_scaled_to_serial(x_hat_k(2));

          print_scaled_to_serial(x_hat_k(3));
        }

        print_scaled_to_serial(pwm_model_value / SERIAL_SCALING_FACTOR);
        print_scaled_to_serial(pwm_real_value / SERIAL_SCALING_FACTOR);

        Serial.println();
      }
    }

    else {
      stop_motor();
    }
  }
}




float get_sine_value(float sine_base, float sine_amplitude, float sine_period_in_sec, float time) {
  float sine_value = sine_base + sine_amplitude * sin(time / sine_period_in_sec * 2 * PI_NUMBER);

  return sine_value;
}



void get_PRBS_64_value(float PRBS_amplitude) {
  int starting_PRBS_counter = 2;
  int shifting_PRBS_counter = 63;

  int first_PRBS_bit_for_xor = 6;
  int second_PRBS_bit_for_xor = 5;

  if (PRBS_counter == 0) {
    PRBS_counter = starting_PRBS_counter;
  }

  int most_left_PRBS_bit = ((PRBS_counter >> first_PRBS_bit_for_xor - 1) ^ (PRBS_counter >> second_PRBS_bit_for_xor - 1)) & 1;
  PRBS_counter = ((PRBS_counter << 1) | most_left_PRBS_bit) & shifting_PRBS_counter;

  float PRBS_value;
  if (PRBS_counter % 2 == 0) {
    PRBS_value = - PRBS_amplitude;
  }
  else {
    PRBS_value = PRBS_amplitude;
  }

  return PRBS_value;
}



float get_dead_zone_compensated_value(float input_pwm_signal) {
  float output_pwm_signal;

  if (input_pwm_signal < - THRESHOLD_PWM_SIGNAL) {
    output_pwm_signal = (input_pwm_signal + THRESHOLD_PWM_SIGNAL) * (MAX_PWM_SIGNAL - MIN_PWM_SIGNAL) / (MAX_PWM_SIGNAL - THRESHOLD_PWM_SIGNAL) - MIN_PWM_SIGNAL;
  }
  else if (input_pwm_signal > THRESHOLD_PWM_SIGNAL) {
    output_pwm_signal = (input_pwm_signal - THRESHOLD_PWM_SIGNAL) * (MAX_PWM_SIGNAL - MIN_PWM_SIGNAL) / (MAX_PWM_SIGNAL - THRESHOLD_PWM_SIGNAL) + MIN_PWM_SIGNAL;
  }
  else {
    output_pwm_signal = 0;
  }

  return output_pwm_signal;
}



void drive_motor(float pwm_real_value) {
  if (pwm_real_value >= 0) {
    digitalWrite(MOTOR_IN1_PIN, HIGH);
    digitalWrite(MOTOR_IN2_PIN, LOW);
  }
  else {
    digitalWrite(MOTOR_IN1_PIN, LOW);
    digitalWrite(MOTOR_IN2_PIN, HIGH);
  }

  analogWrite(MOTOR_ENA_PIN, (int) fabs(pwm_real_value));
}



void stop_motor() {
  digitalWrite(MOTOR_IN1_PIN, LOW);
  digitalWrite(MOTOR_IN2_PIN, LOW);
}



// read encoder A signal when encoder B signal rises
void read_encoder_inc_change() {
  int readed_increment_change = digitalRead(ENCODER_ENCA_PIN);

  // increment position if encoder A signal is high and vice versa
  if (readed_increment_change == 1) {
    readed_increments = readed_increments + 1.0;
  }
  else {
    readed_increments = readed_increments - 1.0;
  }
}



 void read_ultrasound_distance() {
   if (ultrasound_sensor.check_timer()) {
     readed_distance = ultrasound_sensor.ping_result *  MICROSEC_TO_MILLISEC_FACTOR * MILLISEC_TO_SEC_FACTOR * SOUND_VEL_IN_METERS_PER_SEC / 2 ;
   }
 }



void blink_LED() {
  digitalWrite(LED_BUILTIN, HIGH);
  delay((int) (LED_BLINKING_TIME_IN_SEC / MILLISEC_TO_SEC_FACTOR));
  digitalWrite(LED_BUILTIN, LOW);
  delay((int) (LED_BLINKING_TIME_IN_SEC / MILLISEC_TO_SEC_FACTOR));
}



void print_scaled_to_serial(float printing_value) {
  Serial.print(printing_value * SERIAL_SCALING_FACTOR);
  Serial.print(" ");
}
